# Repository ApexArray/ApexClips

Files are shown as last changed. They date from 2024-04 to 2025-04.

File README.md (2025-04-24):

# ApexClips - 3d printer belt mounting

Originally designed for my [fork](https://github.com/ApexArray/Medusa-Toolhead) of [Ch4rlesB's Medusa Toolhead](https://github.com/Ch4rlesB/Medusa-Toolhead/tree/main), but I think this design deserves its own repo now.

This solution aims to be a zero-comporomise method of mounting belts to 3d printer toolheads.

- **Lightweight:** No screws or heat inserts required.
- **Strong:** Tested up to 40 lbs before failure.
- **Low-profile:** End tabs are less than 2mm thick, so they shouldn't interfere with X homing.
- **Easy to assemble:** No need to disassemble the toolhead or fight with zip ties.
- **Tool-less:** Although installation is easier with pliers/tweezers if you have fat fingers like me.
- **Adaptable:** Includes a [step file](./cutout%20tool/Cutout%20Tool%20(v0.1).step) cutout tool, so it can be easily adapted to other toolheads.

## Installation

Insert the belt into the slot, and slide in the printable clip to hold it in place.

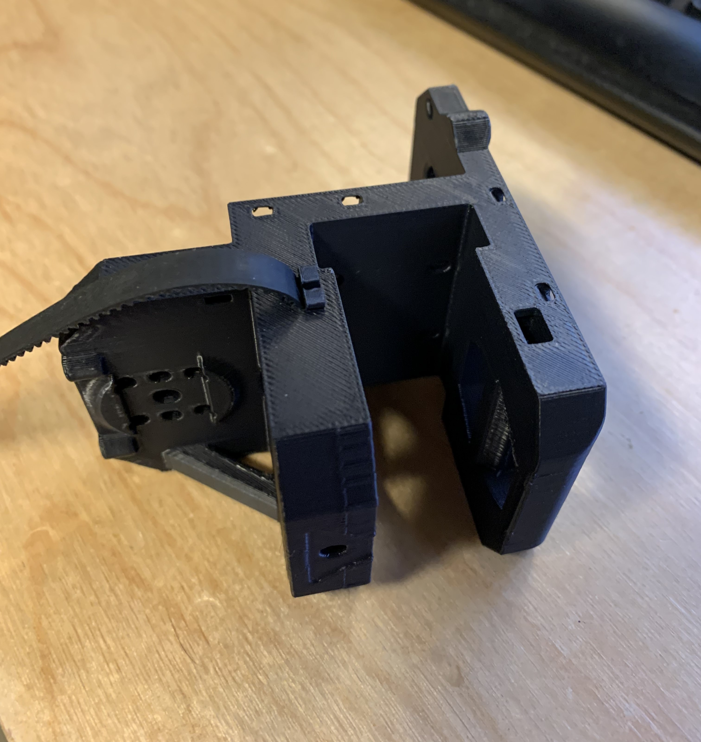
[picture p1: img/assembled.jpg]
assembled


Here it is holding 20lbs

Weight test (20lbs)

[RMRRF 2024: Quick Demonstration](https://twitter.com/Fabreeko_Hector/status/1782216324544115053)

**TIP:** It can be tricky when the clip needs to go between the belt and the gantry (teeth facing outward). Try holding the belt with one hand and insert the clip using tweezers or pliers.

## Try it out

I included a small "test body", so you don't need to print a whole toolhead to test the clips.

Important slicer settings:

- Perimeters: 3+
- Perimeter width: 0.45mm
- External perimieter width: 0.4mm

Print the STLs, install a belt and see if you can pull it out!

## FAQ

### How does it work?

The belt teeth sit in grooves on the inside of the toolhead. Since the belt must first move in the X direction (backing out of the grooves) before it can move in the Y direction (sliding out of the slot), we simply occupy the space behind the belt to keep it in the grooves.

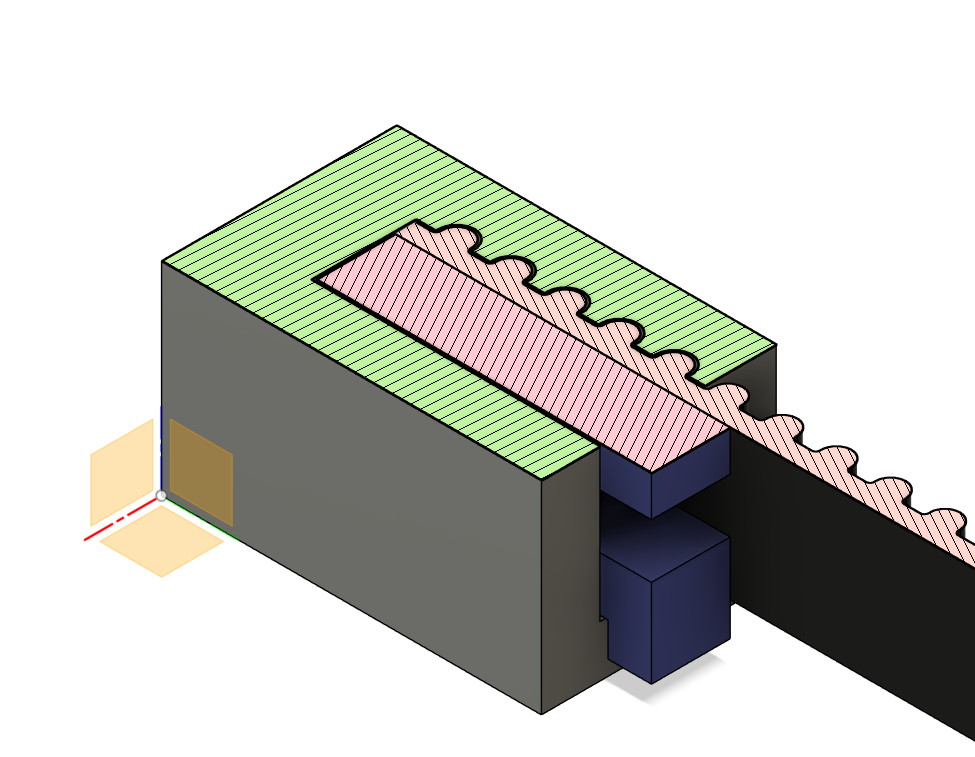
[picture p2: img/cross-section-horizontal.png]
Horizontal cross section

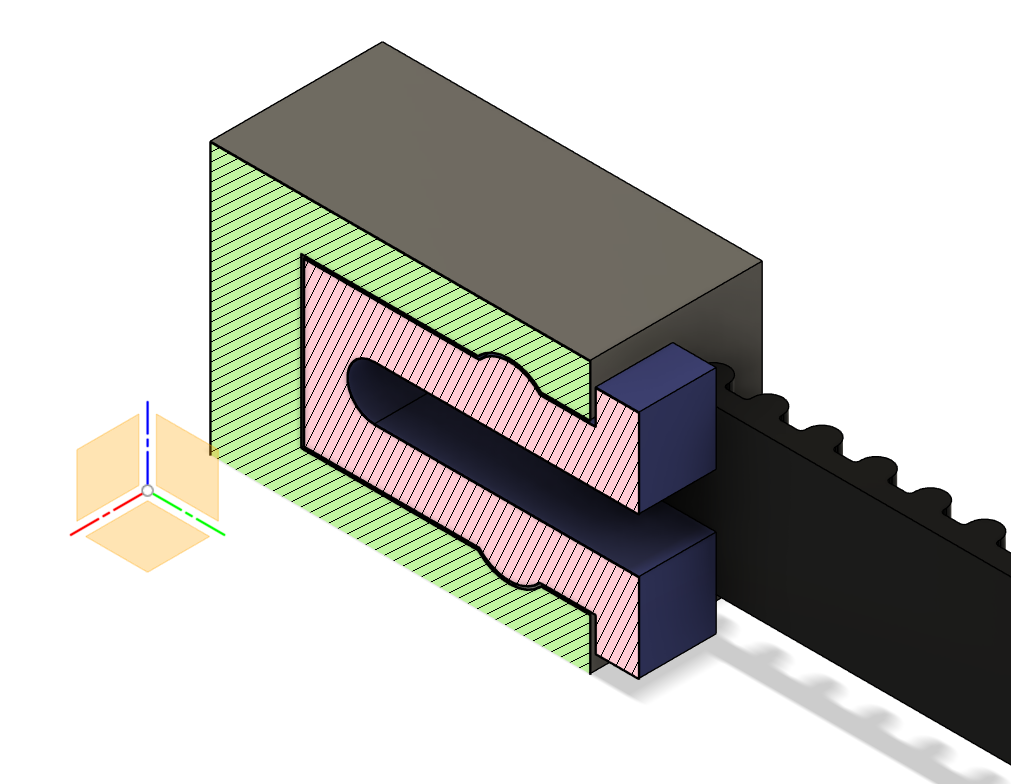
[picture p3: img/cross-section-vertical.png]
Vertical cross section


### Can I use this in my toolhead?

Please do! Send me a link so I can check it out.

### Why these specific dimensions?

The arms are wide enough for three full walls. This seemed to be the happy medium for flexiibility and durability.

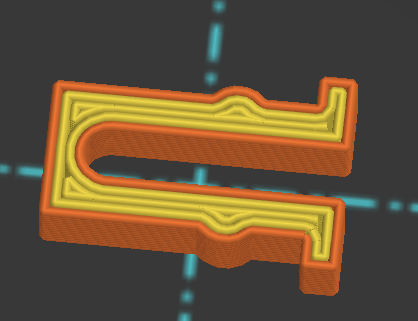
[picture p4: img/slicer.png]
Slicer


The mount is strong enough with just three teeth, but I decided on five teeth for extra reliability.

### The mounts failed and my belt came out!

Make sure the belt is inserted deep enough to engage all five teeth. It might help to mark the belt so you know when you've inserted it to the right depth.

If it still doesn't hold, try printing the clips at a slightly larger scale.

### Does it hold up over time?

Great question! I've had zero failures so far, but I sadly don't have much printing time with them because I'm always taking my printer apart to test new things. Please share your results if you decide to use this method.

## Feedback and Suggestions

Feel free to open a PR or give me a shout on Discord @Apex3d.

## TODO

- Beta testing - any volunteers? 🙂
- Add a flush-mount version (just need to find a way to get the clip out after installation).
- Make an installation helper tool (for the tricky spots).
- Re-design everything in FreeCAD/Ondsel.
- Get this method into every toolhead possible.

## Inspiration

Heavily inspired by [@ChipCE](https://github.com/ChipCE)'s awesome panel clips from the [SnakeOil-XY](https://github.com/SnakeOilXY/SnakeOil-XY/tree/master).

## LICENSE

All files released under [GNU General Public License v3.0](./LICENSE.md).

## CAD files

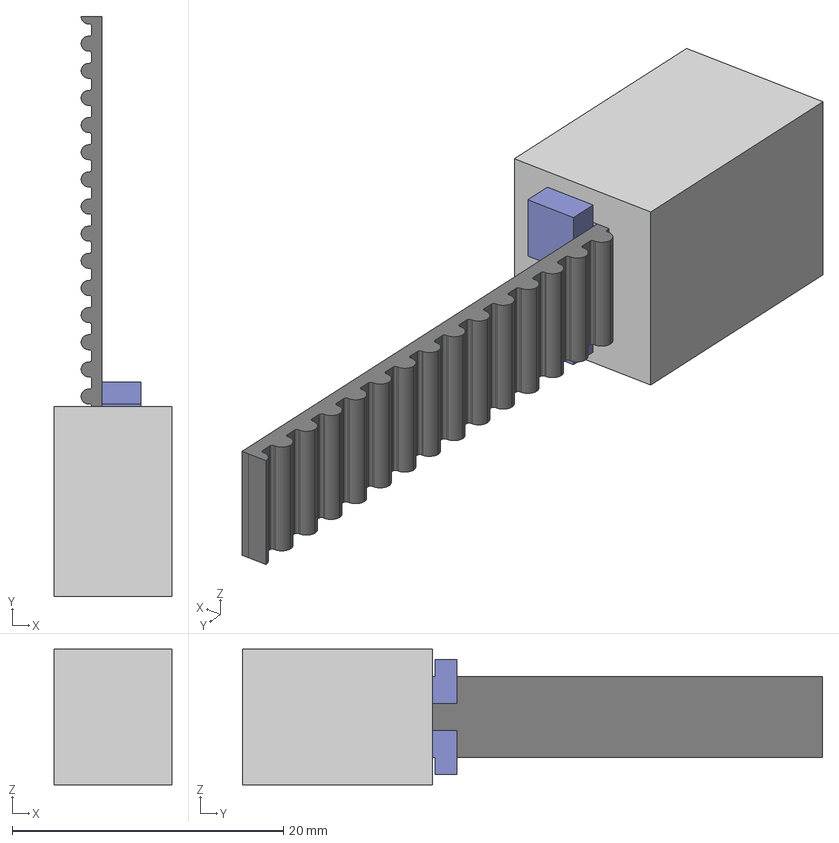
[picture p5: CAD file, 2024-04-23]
src/ApexClip Main (v0.1).step
8.66 x 42.7 x 10.0 mm
test body
GT2 Belt 6mm x 40mm v1
beltClip

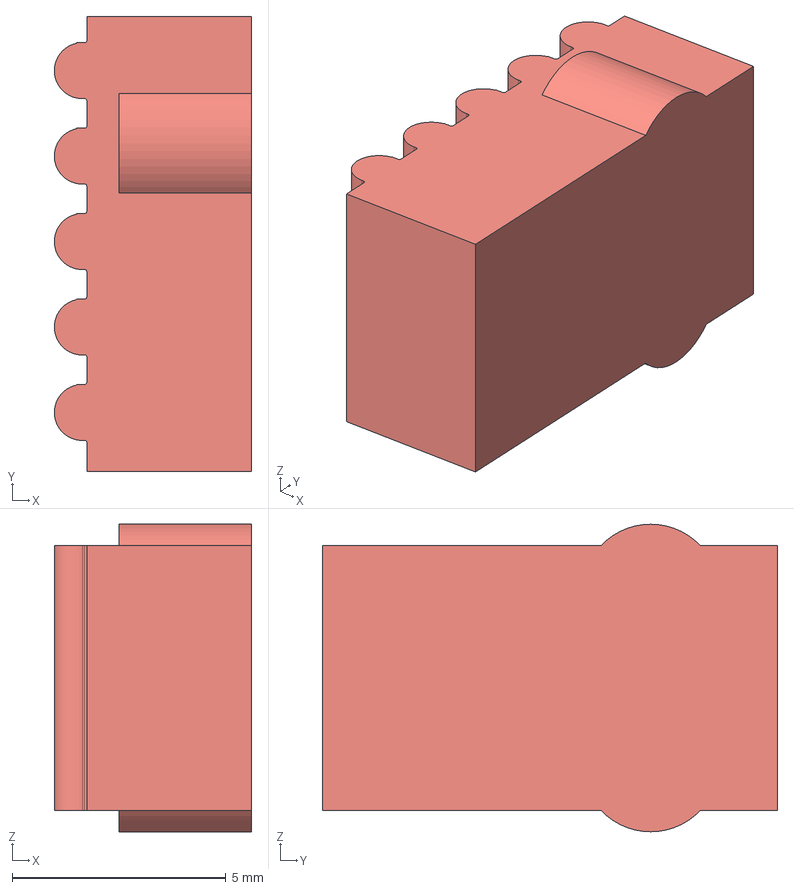
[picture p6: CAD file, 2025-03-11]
cutout tool/Cutout Tool (v0.1).step
4.62 x 10.7 x 7.20 mm

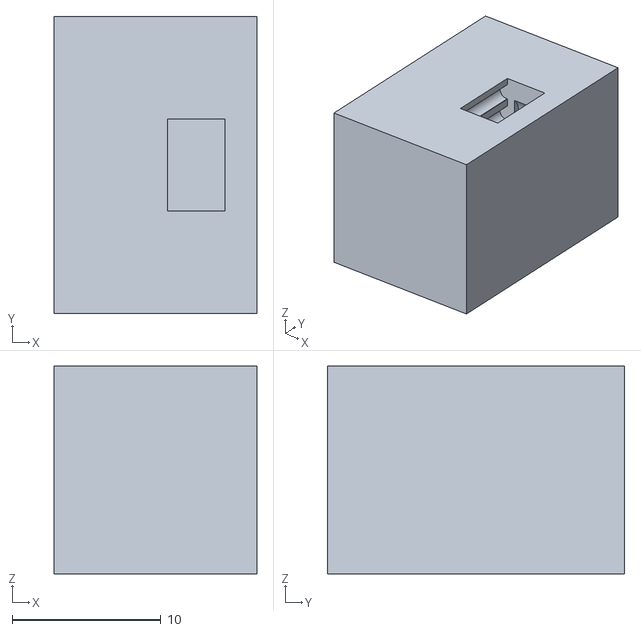
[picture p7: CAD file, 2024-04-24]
stl/test body - large.stl
13.7 x 20.0 x 14.0

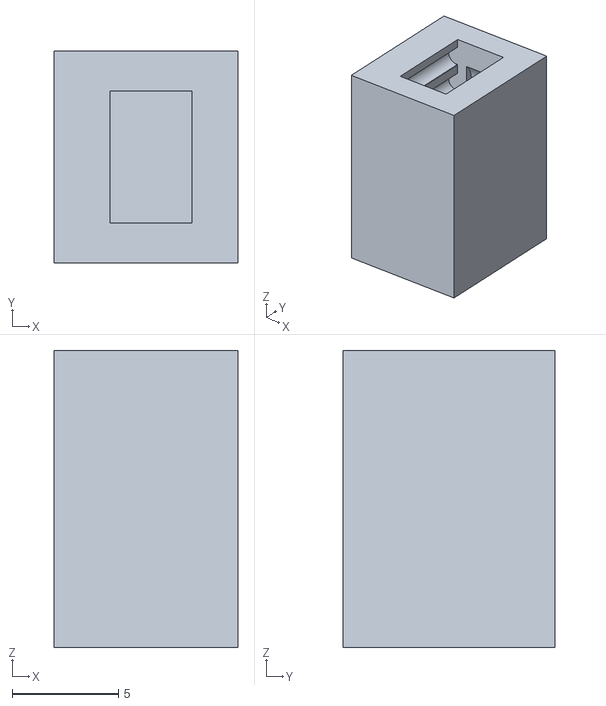
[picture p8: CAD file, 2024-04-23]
stl/test body - small.stl
8.66 x 10.0 x 14.0

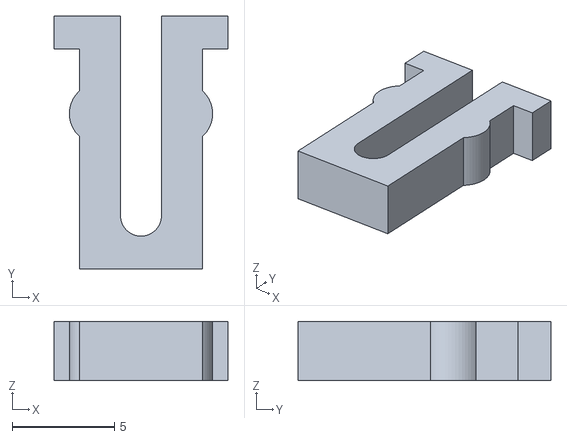
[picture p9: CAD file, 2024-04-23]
stl/ApexClip (v0.1).stl
8.50 x 12.4 x 2.90

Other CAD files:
src/ApexClip Main (v0.1).f3d

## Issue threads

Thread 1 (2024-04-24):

Cutout Tool is an empty STEP file

EllaFoxo, 2024-04-24:
Really love this, saw it on the RMRRF video so cheers!

Just tried to load the cutout tool in Fusion and it was empty hah

vvuk, 2025-03-11:
+1! Was about to use these clips to fix a too-short-belt problem alas!

ApexArray, 2025-03-11:
Sorry about that, not sure what happened! Fixed in the latest commit.

Closed 2025-03-11.

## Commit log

2024-04-23 v0.1 release
    [ApexClip (v0.1).stl, ApexClip Main (v0.1).f3d, ApexClip Main (v0.1).step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]
2024-04-24 add larger test body
    [test body - large.stl, test body - small.stl]
2025-03-11 fix empty cutout tool STEP file
    [Cutout Tool (v0.1).step]
